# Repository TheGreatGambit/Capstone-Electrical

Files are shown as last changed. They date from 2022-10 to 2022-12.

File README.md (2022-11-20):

# The Great Gambit &mdash; Electrical

<!-- Buttons that link to the associated repos, uncomment all but this repo -->
<div align="center">
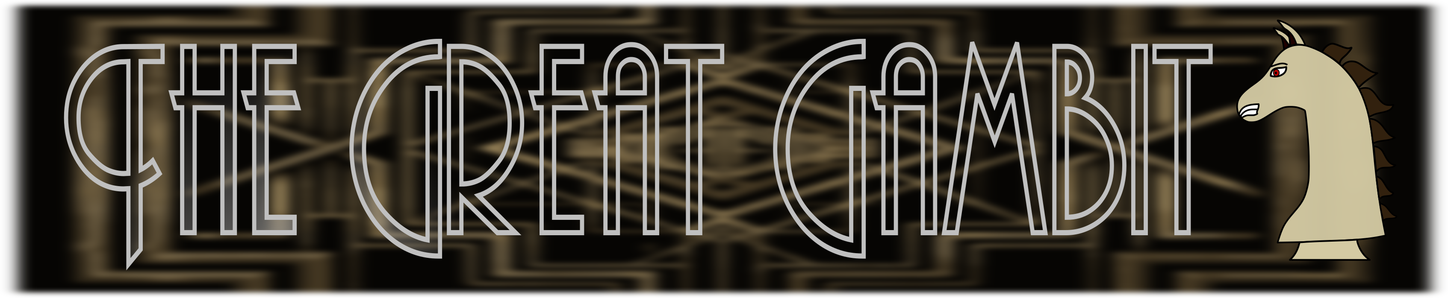
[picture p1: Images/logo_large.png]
The Great Gambit Logo
    
    <a href="https://cadlab.io/project/25988/main/files">
        CadLab Logo
    </a>
    <!-- <a href="https://github.com/TheGreatGambit/Capstone-Electrical">
        <img src="https://github.com/TheGreatGambit/Capstone-Electrical/blob/main/Images/logo_electrical_small.png" alt="Electrical Logo - Small" style="height:40px;width:200px">
    </a> -->
    <a href="https://github.com/TheGreatGambit/Capstone-Software">
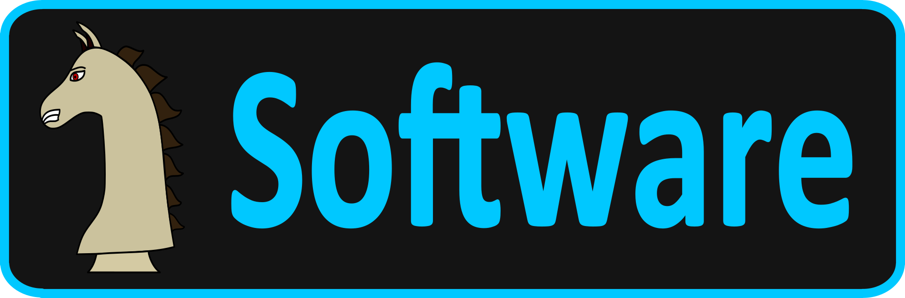
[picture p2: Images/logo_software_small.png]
Software Logo - Small
        
    </a>
    <a href="https://github.com/TheGreatGambit/Capstone-Mechanical-CAD">
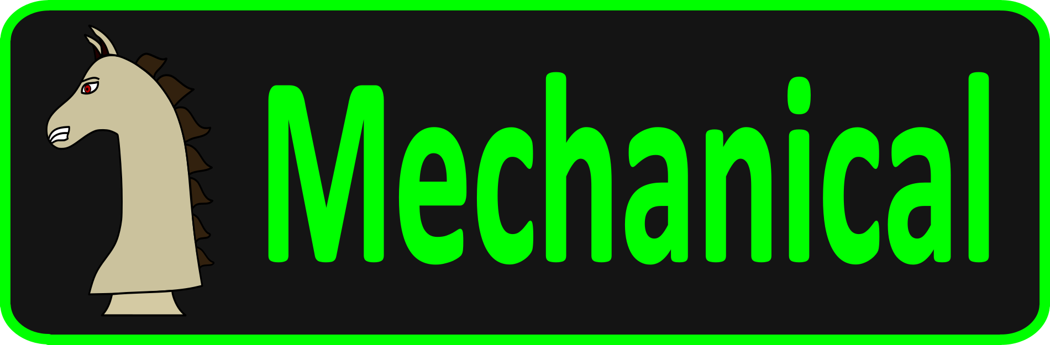
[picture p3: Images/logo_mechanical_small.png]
Mechanical Logo - Small
        
    </a>
    <a href="https://github.com/TheGreatGambit/Capstone-PyChess">
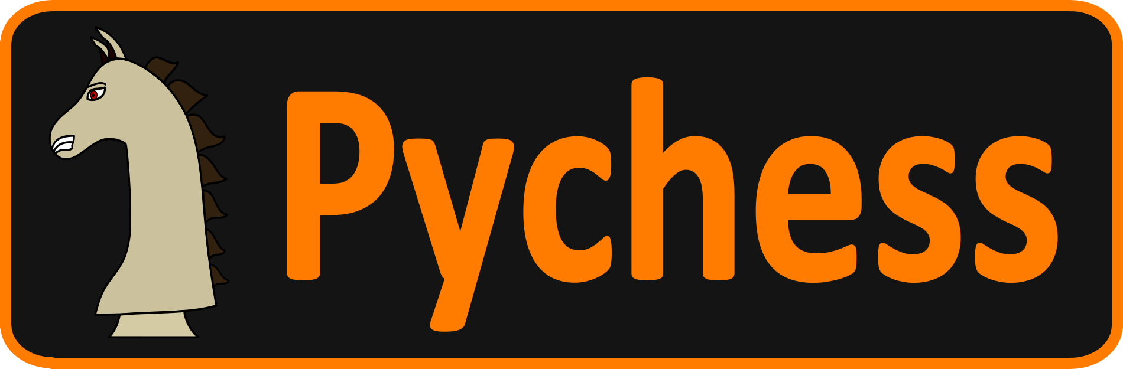
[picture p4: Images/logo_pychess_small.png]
PyChess Logo - Small
        
    </a>
</div>

<!-- Brief overview of this repo -->
## Overview
This project aims to create an autonomous robot capable of playing an intelligent, over-the-board game of chess against a human opponent. The system uses a three-axis, cantilevered, overhead gantry to move parallel to the chess board. Each axis is driven by a stepper motor, the horizontal axes using belts and the vertical axis using a rack and pinion. A crosspoint array of reed switches embedded in the physical chess board allows for piece detection, and with software record of the board state, piece recognition. This system is orchestrated by an [MSP432E401Y](https://www.ti.com/product/MSP432E401Y) microcontroller, with chess moves being pulled from the open-source [Stockfish](https://github.com/official-stockfish/Stockfish) chess engine, running on a [Raspberry Pi 3A+](https://www.raspberrypi.com/products/raspberry-pi-3-model-a-plus/). All communication between the Raspberry Pi and MSP432 is done through a universal asynchronous receiver-transmitter (UART) serial connection.

This repository contains all schematic and PCB files for the system, generated in [KiCad](https://www.kicad.org/). Files can be graphically viewed at [CADLab](https://cadlab.io/project/25988/main/files). In this document, `<LGR>` will indicate *your* local path to the GIT repo.

## Setup
1. Clone this repo onto your local machine.
2. Open `<LGR>/Boards/Main_Board/_Top_Level/Main_Board.kicad_pro` with KiCad to view the main project.
3. In KiCad, open `Main_Board.kicad_sch` to view the schematic, or `Main_Board.kicad_pcb` to view the PCB.

## Adding a Board (Project)
1. Create the following new directories:
    - `<LGR>/Boards/<YOUR_BOARD_NAME>`
    - `<LGR>/Boards/<YOUR_BOARD_NAME>/_DFM`
    - `<LGR>/Boards/<YOUR_BOARD_NAME>/_DFM/Gerber`
    - `<LGR>/Boards/<YOUR_BOARD_NAME>/_Top_Level`
2. Open KiCad
3. Select `File`->`New Project`
4. A `Create New Project` window will pop up. In the window, navigate to `<LGR>/Boards/<YOUR_BOARD_NAME>/_Top_Level`
5. Enter the file name `<YOUR_BOARD_NAME>.kicad_pro` and click `Save`

## Adding a Subsheet in an Existing Board
1. Create a new directory: `<LGR>/Boards/<YOUR_BOARD_NAME>/<SUBSHEET_NAME>`
2. Open `<LGR>/Boards/<YOUR_BOARD_NAME>/_Top_Level/<YOUR_BOARD_NAME>.kicad_sch` in the KiCad Schematic Editor
3. Select `Place`->`Add Sheet`
4. Click to place the symbol
5. A `Sheet Properties` window will pop up. Add the following entry:
    - Sheet Name: `<DESCRIPTIVE_NAME>`, Sheet File: `../<SUBSHEET_NAME>/<COMPONENT_NAME>.kicad_sch`
6. Right click the component and select `Import Sheet Pin` to place the hierarchical labels

## Installing External Libraries
*Note: We no longer use a custom path for project libraries. We instead use relative paths from `${KIPRJMOD}`*
1. **Install the library:**
    1. Download an external library
        - Ex: A model for the [DRV8824QPWPRQ1](https://www.mouser.com/ProductDetail/Texas-Instruments/DRV8824QPWPRQ1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) can be found under 'ECAD Model' 
    2. Unzip the download to get a `*.epw` file
    3. Download the [Library Loader](https://ms.componentsearchengine.com/pcb-libraries.php) tool from Mouser
    4. Register/login to the Library Loader tool
    5. Click `Open ECAD Model` and select the downloaded `*.epw` file
    6. By default the output is in `~/Downloads/LIB_GET.zip`. Unzip it
    7. Copy the unzipped contents into: `<LGR>/Project_Libraries/<LIBRARY_NAME>`
2. **Import the symbol:**
    1. In the KiCad Schematic Editor, go to: `Preferences`->`Manage Symbol Libraries`->`Project Specific Libraries`
    2. Add the following entry by clicking the `+` button:
        - Nickname: `<LIBRARY_NAME>`, Library Path: `${KIPRJMOD}/../../../Project_Libraries/<LIBRARY_NAME>/KiCad/<LIBRARY_NAME>.lib`
    3. Select `Migrate Libraries`
    4. Place the device in KiCad by going to `Place`->`Add Symbol` and search for `<LIBRARY_NAME>`
3. **Add the footprint:**
    1. In the KiCad PCB Editor, go to: `Preferences`->`Manage Footprint Libraries`->`Project Specific Libraries`
    2. Add the following entry by clicking the `+` button:
        - Nickname: `<LIBRARY_NAME>`, Library Path: `${KIPRJMOD}/../../../Project_Libraries/<LIBRARY_NAME>/KiCad`
4. **Update the symbol field to make exporting the BOM easier:**
    1. Right click on the symbol and click `Properties`
    2. Click `Edit Library Symbol`. This should open a symbol editing window.
    3. Go to `File -> Symbol Properties`
    4. Use the `+` button to add the fields `Datasheet`, `Manufacturer's Part Number`, `Digikey Part Number`, `Mouser Part Number`, `Digikey Link`, and `Mouser Link` in that order (with that exact spelling/capitalization)
        - The `Datasheet` should be a URL to the datasheet, and the `Digikey link` and `Mouser link` fields should be links to the part's product page
    5. Uncheck the `Show` field for everything except the `Reference` and `Value` fields
    6. If the part has a meaningful value (e.g., a 10k resistor), add that value in the `Value` field
    7. In the `Footprint` field, select the folder icon and search for `<LIBRARY_NAME>` in the popup
    8. Double click the result to associate the footprint you imported with the symbol you imported
        - Note: The footprint field might show something like `<LIBRARY_NAME>:<SEEMINGLY_RANDOM_STRING>`, this is okay
    7. Click `Ok` and close the library editor
    8. In the schematic, either right click the symbol and select `Update` or delete and re-add the symbol. The fields should now be included correctly

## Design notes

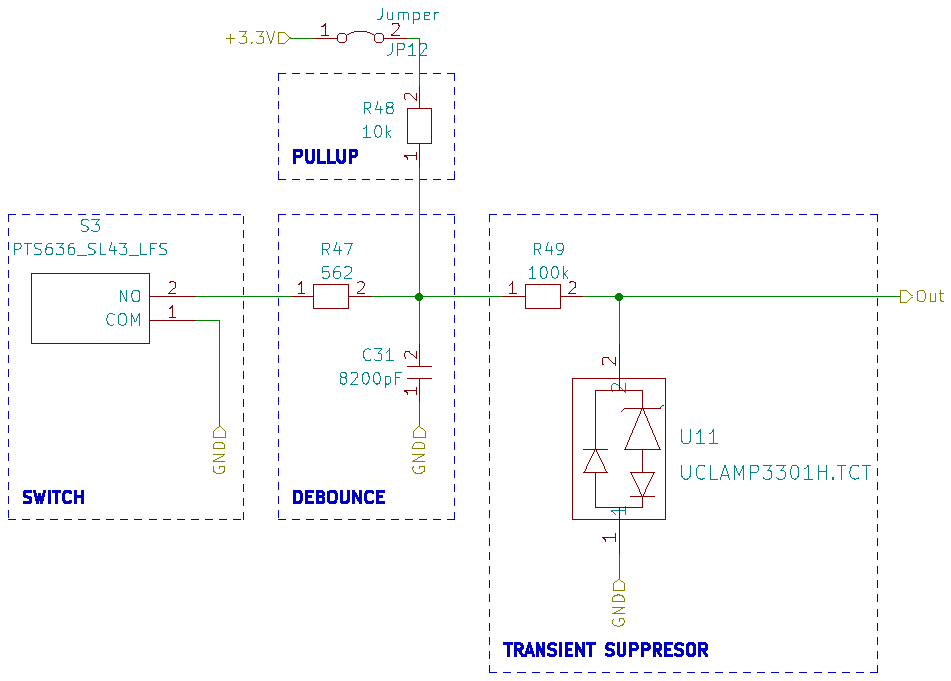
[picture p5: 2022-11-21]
Images/Main_Board/Button_Subsystem.PNG

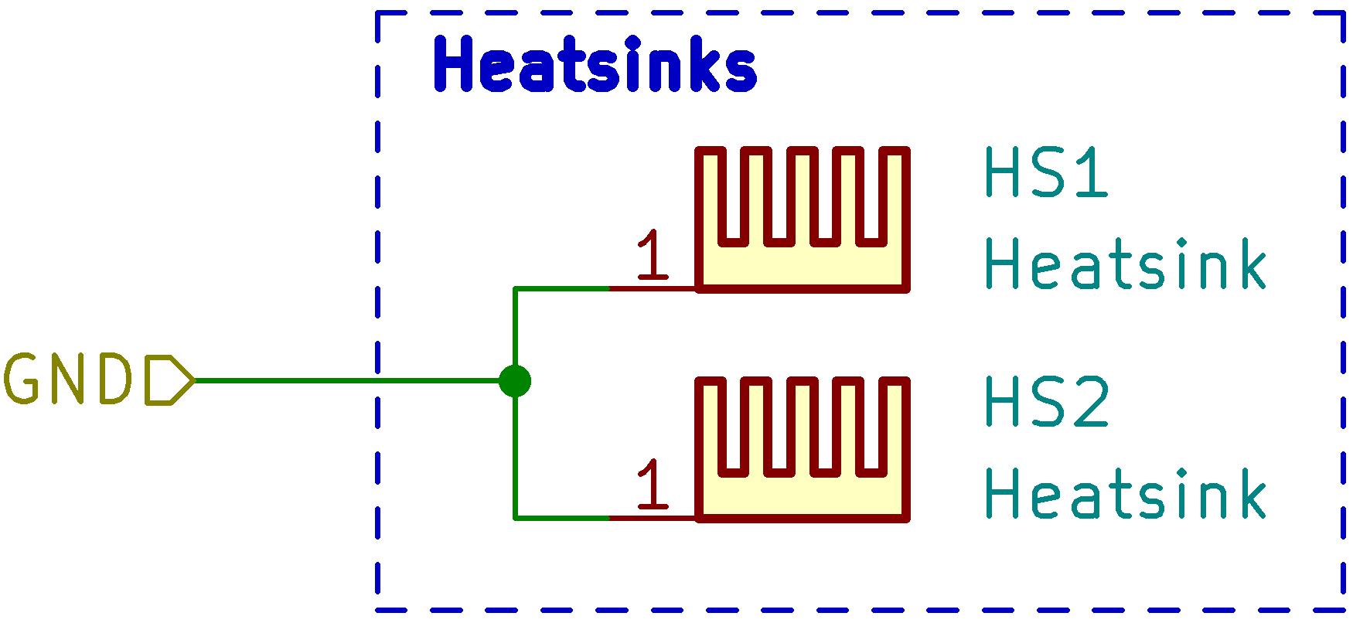
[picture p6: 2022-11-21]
Images/Main_Board/Heatsink_Subsystem.PNG

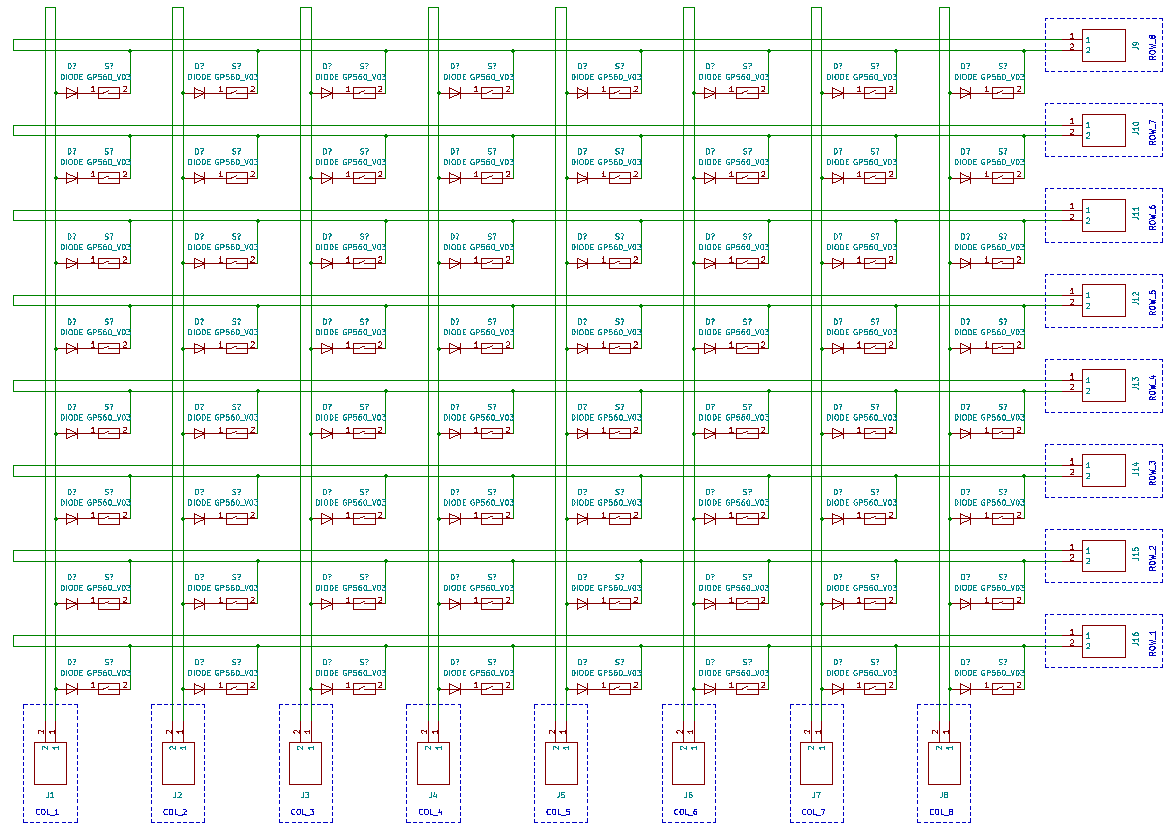
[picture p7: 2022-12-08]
Images/Sensor_Board_17x17/_Top_Level.PNG

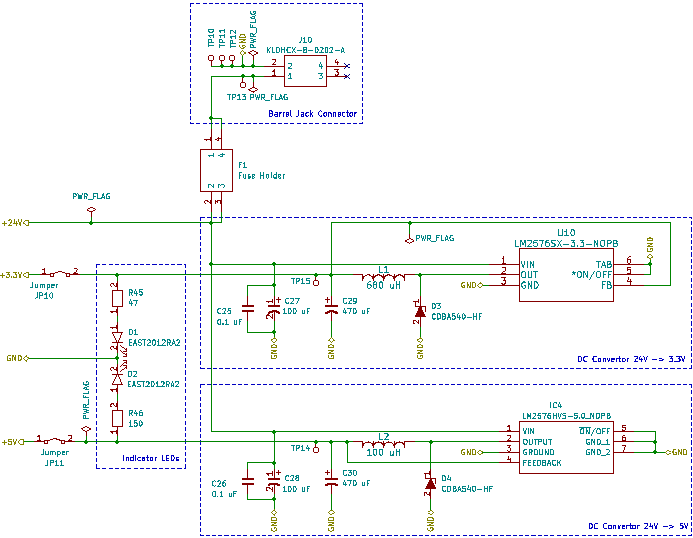
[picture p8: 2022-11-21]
Images/Main_Board/Power_Subsystem.PNG

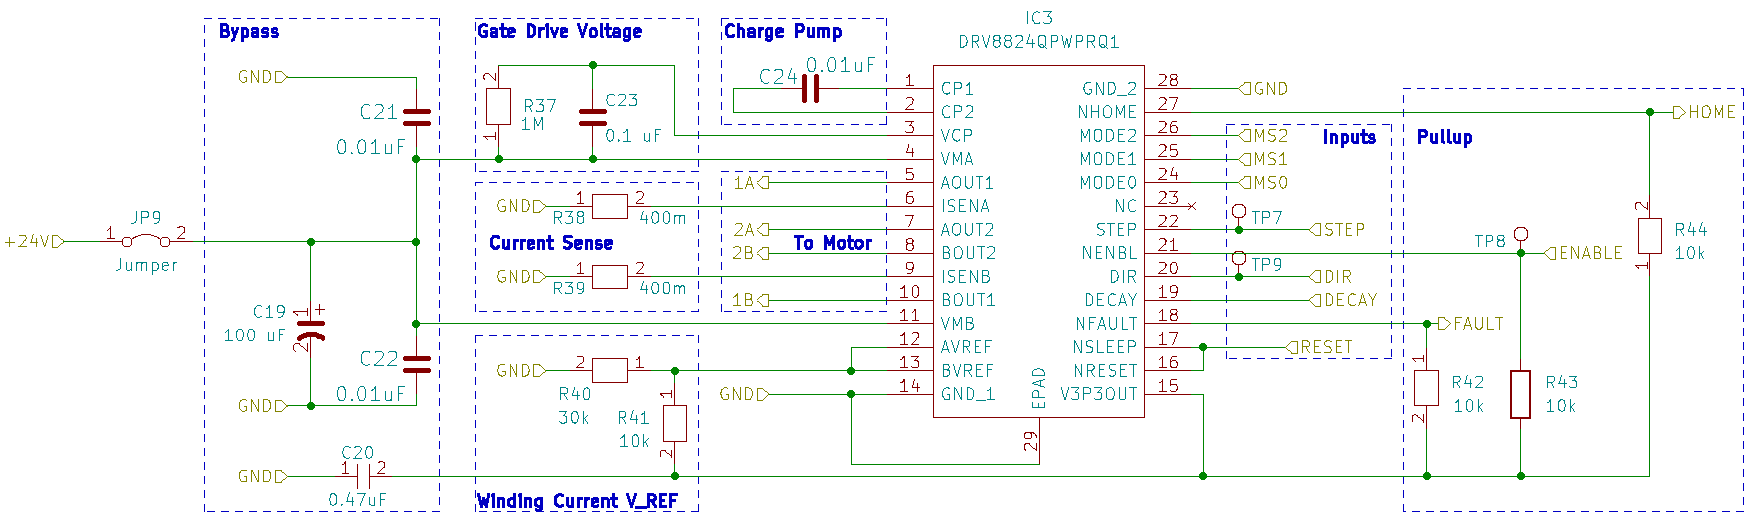
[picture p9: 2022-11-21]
Images/Main_Board/Stepper_Subsystem.PNG

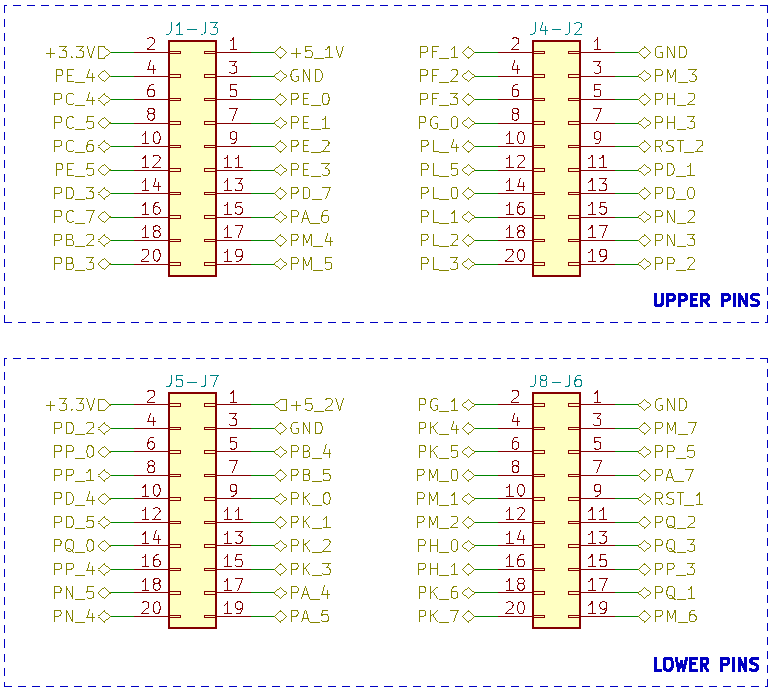
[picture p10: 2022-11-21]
Images/Main_Board/MSP_Subsystem.PNG

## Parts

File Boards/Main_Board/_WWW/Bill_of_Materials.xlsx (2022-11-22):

The Great Gambit PCB
REV 21
Line | Quantity | Reference | Value | MANU PART # | MANU
1 | 5 | C1, C7, C19, C27, C28 | 100 uF | 860020573008 | Würth Elektronik
2 | 3 | C2, C8, C20 | 0.47uF | C1812X474K2RACAUTO | KEMET
3 | 8 | C5, C11, C23, C25, C26, C33-C35 | 0.1 uF | CL10B104KB8NNNC | Samsung Electro-Mechanics
4 | 9 | C3, C4, C6, C9, C10, C12, C21, C22, C24 | 0.01uF | CK05BX103K | KYOCERA AVX
5 | 12 | C13, C14, C15, C16, C17, C18, C31, C32, C37-C40 | 8200pF | C1210C822K2RACAUTO | KEMET
6 | 3 | C29, C30, C36 | 470 uF | EEE-FP1E471AP | Panasonic Electronic Components
7 | 2 | D1, D2 |  | EAST2012RA2 | Everlight Electronics Co Ltd
8 | 2 | D3, D4 |  | CDBA540-HF | Comchip Technology
9 | 1 | F1 |  | 3588 | Keystone Electronics
10 | 2 | HS1, HS2 |  | ATS-52150P-C1-R0 | Advanced Thermal Solutions Inc.
11 | 3 | IC1-IC3 |  | DRV8824QPWPRQ1 | Texas Instruments
12 | 1 | IC4 |  | LM2576HVS-5.0/NOPB | Texas Instruments
13 | 1 | IC5 |  | BD62130AEFJ-E2 | Rohm Semiconductor
14 | 1 | J1 | DNI | 302-S101 | On Shore Technology Inc.
15 | 10 | J2, J7-J9, J11, J20-J24 | DNI | OQ0212500000G | Amphenol Anytek
16 | 11 | J3, J4, J5, J12, J13, J14, J15, J16, J17, J18, J19 | DNI | OQ0432500000G | Amphenol Anytek
17 | 4 | J1-J3, J4-J2, J5-J7, J8-J6 | DNI | PPTC102LFBN-RC | Sullins Connector Solutions
18 | 1 | J6 | DNI | USB1130-15-A | GCT
19 | 1 | J10 | DNI | KLDHCX-8-0202-A | Kycon, Inc.
20 | 21 | JP1, JP2, JP3, JP4, JP5, JP6, JP7, JP8, JP9, JP10, JP11, JP12, JP13, JP14, JP15, JP16, JP17, JP18, JP19, JP20, JP21 | DNI | PH1-02-UA | Adam Tech
21 | 1 | L1 | 680 uH | SRR1210-681M | Bourns Inc.
22 | 1 | L2 | 100 uH | PA4344.104NLT | Pulse Electronics
23 | 1 | LED1 |  | HV-5RGB25 | Inolux
24 | 3 | R1, R9, R37 | 1M | TNPV08051M00BEEA | Vishay Dale
25 | 6 | R2, R3, R10, R11, R38, R39 | 400m | WSL2010R4000FEA | Vishay Dale
26 | 3 | R4, R12, R40 | 30k | ERJ-PB6B3002V | Panasonic Electronic Components
27 | 37 | R5, R6, R8, R13, R14, R16, R20, R23, R26, R29, R32, R35, R41, R42, R44, R48, R51, R58-R73, R75, R78, R81, R84 | 10k | RMCF1206FT10K0 | Stackpole Electronics Inc
28 | 3 | R7, R15, R43 | 10k
29 | 2 | R17, R18 | 2.2 k | CF14JT2K20 | Stackpole Electronics Inc
30 | 12 | R19, R22, R25, R28, R31, R34, R47, R50, R74, R77, R80, R83 | 562 | CR0402-FX-5620GLF | Bourns Inc.
31 | 12 | R21, R24, R27, R30, R33, R36, R49, R52, R76, R79, R82, R85 | 100k | RCV2512100KFKEGAT | Vishay Dale
32 | 1 | R45 | 47 | CHP2512AFX-47R0ELF | Bourns Inc.
33 | 1 | R46 | 150 | SDR03EZPF1500 | Rohm Semiconductor
34 | 5 | R53, R54, R55, R56, R57 | 270 | SDR10EZPJ271 | Rohm Semiconductor
35 | 1 | R86 | 1.2k
36 | 3 | S1, S2, S3 |  | PTS636 SL43 LFS | C&K
37 | 17 | TP1, TP2, TP3, TP4, TP5, TP6, TP7, TP8, TP9, TP10, TP11, TP12, TP13, TP14, TP15, TP16, TP17 | DNI | 5010 | Keystone Electronics
38 | 16 | U1, U2, U3, U4, U5, U6, U8, U9, U11, U12, U13, U14, U17, U18, U19, U20 |  | UCLAMP3301H.TCT | Semtech Corporation
39 | 1 | U7 |  | JS102011SCQN | C&K
40 | 1 | U10 |  | LM2576SX-3.3/NOPB | Texas Instruments
41 | 2 | U15, U16 |  | SN74LV4051ATPWRQ1 | Texas Instruments
42 | 1 | U21 |  | RUC002N05T116 | Rohm Semiconductor

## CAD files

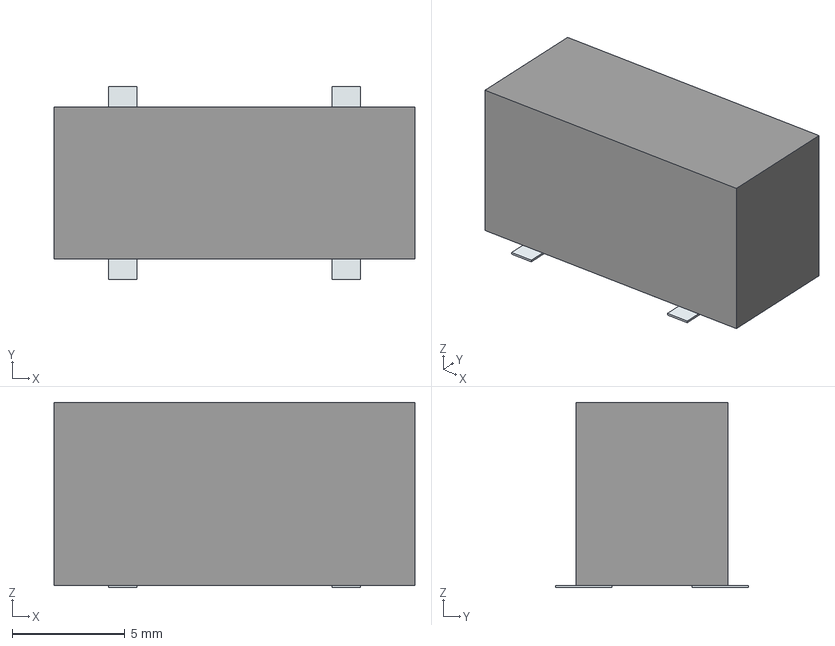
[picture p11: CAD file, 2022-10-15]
Project_Libraries/3588/3588/3D/3588.stp
16.0 x 8.57 x 8.22 mm
Pins

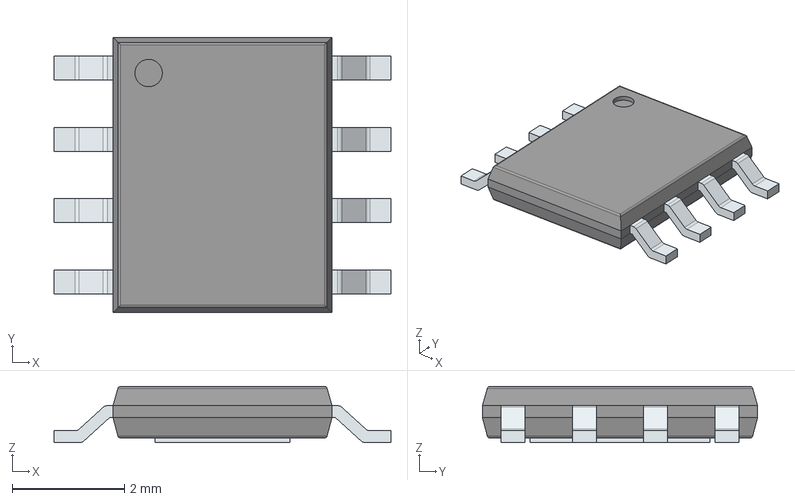
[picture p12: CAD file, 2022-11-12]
Project_Libraries/BD62130AEFJ-E2/BD62130AEFJ-E2/3D/BD62130AEFJ-E2.stp
6.00 x 4.90 x 1.00 mm
PinsArrayLR
ThermalPad

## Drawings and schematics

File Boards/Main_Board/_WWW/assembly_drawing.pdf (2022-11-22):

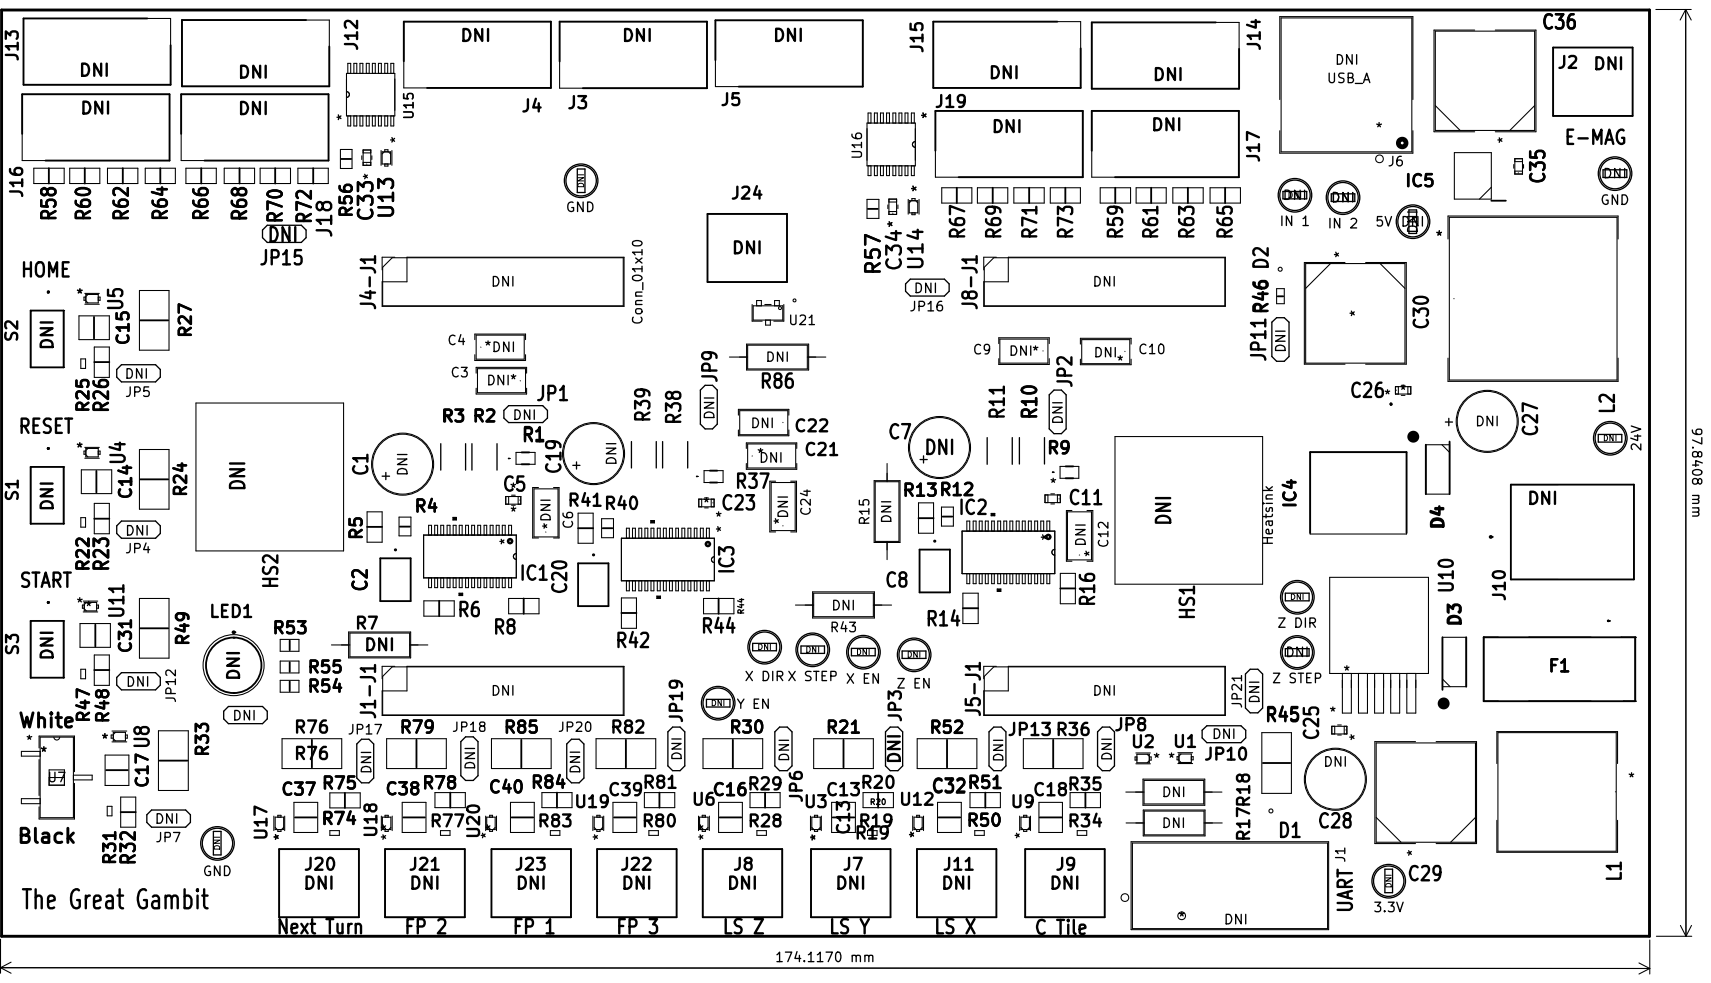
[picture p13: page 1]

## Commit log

2022-10-03 Break top level scheamtic into subsystems. Use DRV8824-Q1 driver chip. Document setup
    [Button.kicad_sch, Button_Template.kicad_sch, Buttons_Full.kicad_sch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]
2022-10-04 Worked on Power supply subsheet
    [Button.kicad_sch, EDI2CAP.CFG, KLDHCX-8-0202-A.stp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]
2022-10-04 Finalize MSP432, stepper, and button subsheets
    [Button.kicad_sch, EDI2CAP.CFG, LED.kicad_sch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]
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2022-10-04 Add gitignore, fix stepper subsystem
    [LED.kicad_sch, Stepper_Driver.kicad_sch, Top_Level.kicad_sch]
2022-10-04 Changed the DC convertor circuit
    [PowerSupply.kicad_sch]
2022-10-04 Add digikey/mouser components to stepper and button subsystems
    [Button.kicad_sch, C1210C822K2RACAUTO.stp, C1812X474K2RACAUTO.stp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]
2022-10-05 Added specific components for the power subsheet
    [PowerSupply.kicad_sch, Top_Level.kicad_sch]
2022-10-06 PA4 and PA5 reserved for U3RX and U3TX in top-level schematic
    [Top_Level.kicad_sch]
2022-10-09 Fix LED subsystem, cut unnecessary GPIO connections, add sheets for remaining subsystems
    [EDI2CAP.CFG, Electromagnet.kicad_sch, LED.kicad_sch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]
2022-10-09 Switched the pins on the barrel jack connector
    [Button.kicad_sch, LED.kicad_sch, PowerSupply.kicad_sch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]
2022-10-09 Added footprint for the switches
    [Button.kicad_sch, Top_Level.kicad_pcb, Top_Level.kicad_sch]
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2022-10-09 Fix all footprints and symbols, import to PCB
    [PowerSupply.kicad_sch, Top_Level.kicad_pcb, Top_Level.kicad_sch]
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2022-10-09 Added circuitry for the Pi subsystem
    [Button.kicad_sch, PiConnector.kicad_sch, Stepper_Driver.kicad_sch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]
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2022-10-09 Fix MSP connector spacing
    [Button.kicad_sch, LED.kicad_sch, LimitSwitch.kicad_sch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]
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2022-10-10 placed switched + buttons
    [Top_Level.kicad_pcb]
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2022-10-12 Cleanup files so ERC passes
    [Button.kicad_sch, LimitSwitch.kicad_sch, MSP432E401Y.kicad_sch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]
2022-10-12 Fixed entire BOM for all components
    [Button.kicad_sch, LED.kicad_sch, LimitSwitch.kicad_sch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]
2022-10-12 Adjusted the Pi subsystem
    [Button.kicad_sch, LimitSwitch.kicad_sch, MSP432E401Y.kicad_sch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]
2022-10-12 Fix annotations, add test points
    [Button.kicad_sch, LED.kicad_sch, LimitSwitch.kicad_sch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]
2022-10-12 Add screenshots of each subsystem
    [Button.kicad_sch, LimitSwitch.kicad_sch, MSP432E401Y.kicad_sch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]
2022-10-15 Added 5V power supply
    [Button.kicad_sch, CDBA540-HF.stp, LimitSwitch.kicad_sch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]
2022-10-15 Added extra bypass caps to the power supply
    [Button.kicad_sch, LimitSwitch.kicad_sch, PowerSupply.kicad_sch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]
2022-10-15 Added a fuse and fixed ERC
    [3588.stp, Button.kicad_sch, LimitSwitch.kicad_sch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]
2022-10-15 Added jumpers to the 3.3 and 5V lines
    [PiConnector.kicad_sch, PowerSupply.kicad_sch, Stepper_Driver.kicad_sch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]
2022-10-15 Redo sensor network, redo MSP432 connections, redo LED subsystem, add shunts throughout, ERC still passes
    [Button.kicad_sch, LED.kicad_sch, LimitSwitch.kicad_sch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]
2022-10-15 Added LEDs to the power supply
    [Button.kicad_sch, LimitSwitch.kicad_sch, PowerSupply.kicad_sch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]
2022-10-16 Added electromagnet circuit and adjusted the bypass caps
    [DRV8210DRLR.stp, Electromagnet.kicad_sch, PowerSupply.kicad_sch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]
2022-10-16 Resolve misconfigured components, replace PCB from now completed schematic
    [Button.kicad_sch, Electromagnet.kicad_sch, LED.kicad_sch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]
2022-10-16 Swapped pins on the barrel jack
    [Button.kicad_sch, LimitSwitch.kicad_sch, PowerSupply.kicad_sch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]
2022-10-16 Layed out power supply
    [LimitSwitch.kicad_sch, Stepper_Driver.kicad_sch, Top_Level.kicad_pcb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]
2022-10-21 Added USB connector for the pi
    [Button.kicad_sch, LimitSwitch.kicad_sch, Stepper_Driver.kicad_sch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]
2022-10-21 Swapped TVS Diodes
    [Button.kicad_sch, LimitSwitch.kicad_sch, PiConnector.kicad_sch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]
2022-10-21 Relayed out the power supply and stepper drivers
    [Button.kicad_sch, LimitSwitch.kicad_sch, PiConnector.kicad_sch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]
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2022-10-21 Layed out stepper connectors and test points
    [PiConnector.kicad_sch, Top_Level.kicad_pcb, Top_Level.kicad_sch]
2022-10-22 Redo pinout, finish pcb layout (no traces)
    [Button.kicad_sch, Electromagnet.kicad_sch, LED.kicad_sch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]
2022-10-23 Add GND plane, GND major ICs
    [Top_Level.kicad_pcb]
2022-10-23 Adjust stepper placement for heatsinks
    [Top_Level.kicad_pcb]
2022-10-25 Added heatsink footprints in approx. location
    [Top_Level.kicad_pcb]
2022-10-26 Flipped the MSP headers
    [MSP432E401Y.kicad_sch, Top_Level.kicad_pcb, Top_Level.kicad_sch]
2022-10-26 Reordered the sensor network to shorten traces
    [Top_Level.kicad_pcb, Top_Level.kicad_sch]
2022-10-26 Fixed footprint courtyard issues (mostly)
    [Button.kicad_sch, Electromagnet.kicad_sch, LimitSwitch.kicad_sch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]
2022-10-26 Redid the stepper drivers to adhere to TI's layout directions
    [Stepper_Driver.kicad_sch, Top_Level.kicad_pcb, Top_Level.kicad_sch]
2022-10-27 Fix vias for Analog Digital's requirements
    [Button.kicad_sch, Electromagnet.kicad_sch, LimitSwitch.kicad_sch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]
2022-10-27 Fix stepper driver footprints
    [Stepper_Driver.kicad_sch, Top_Level.kicad_pcb, Top_Level.kicad_sch]
2022-10-27 Added stepper traces to connectors
    [Top_Level.kicad_pcb]
2022-10-28 Layed out the user buttons
    [Switch.kicad_sch, Top_Level.kicad_pcb]
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2022-10-28 Placed all the protection components
    [Button.kicad_sch, Electromagnet.kicad_sch, LimitSwitch.kicad_sch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]
2022-10-28 Rearranged connectors to shorten traces
    [Top_Level.kicad_pcb]
2022-10-28 Moved some pins to make routing easier
    [Top_Level.kicad_pcb, Top_Level.kicad_sch]
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2022-10-28 Adjustments in prep for silkscreen
    [Top_Level.kicad_pcb, Top_Level.kicad_sch]
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2022-10-28 Only the truly awful traces left
    [Top_Level.kicad_pcb, Top_Level.kicad_sch]
2022-10-28 KiCad keeps crashing and getting rid of silkscreen
    [Top_Level.kicad_pcb, Top_Level.kicad_sch]
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2022-10-28 All major traces done
    [Top_Level.kicad_pcb, Top_Level.kicad_sch]
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2022-10-28 Finish traces, fix DRC, add gerbers
    [Top_Level.kicad_pcb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]
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2022-10-28 Added polarity to capacitor silkscreens
    [Top_Level.kicad_pcb]
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2022-10-28 Smaller pads on the LED
    [Top_Level.kicad_pcb]
2022-10-28 Silkscreen fixes
    [Top_Level.kicad_pcb]
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2022-10-28 4th times the charm
    [Top_Level.kicad_pcb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]
2022-10-29 New try at FreeDFM
    [Top_Level.kicad_pcb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]
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2022-10-30 Spaced out vias. No show stoppers
    [Top_Level.kicad_pcb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]
2022-10-30 Corrections to the power supply
    [MSP432E401Y.kicad_sch, PowerSupply.kicad_sch, Top_Level.kicad_pcb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]
2022-10-30 Swapped resistors in stepper driver
    [Electromagnet.kicad_sch, PiConnector.kicad_sch, PowerSupply.kicad_sch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]
2022-10-30 Fixed the barrel jack footprint
    [Top_Level.kicad_pcb]
2022-10-30 Changed Pi resistors back to through hole
    [PiConnector.kicad_sch, PowerSupply.kicad_sch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]
2022-10-30 Last? Submission to FreeDFM
    [Top_Level-job.gbrjob]
2022-11-09 Updates from meeting with Powell
    [Top_Level.kicad_pcb]
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2022-11-10 Working on power supply
    [Top_Level.kicad_pcb, Top_Level.kicad_sch]
2022-11-10 Added signal light MOSFET
    [PowerSupply.kicad_sch, Signal_Light.kicad_sch, Stepper_Driver.kicad_sch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]
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2022-11-12 Replace small resistors/capacitors with through-hole; fix DRC aside from electromagnet and MUXes
    [Button.kicad_sch, LED.kicad_sch, LimitSwitch.kicad_sch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]
2022-11-12 Replace MUX/DEMUX; DRC passes aside from electromagnet
    [Electromagnet.kicad_sch, LimitSwitch.kicad_sch, SensorNetwork.kicad_sch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]
2022-11-12 Replaced electromagnet IC and fixed ERC errors with stepper driver
    [BD62130AEFJ-E2.stp, Electromagnet.kicad_sch, SensorNetwork.kicad_sch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]
2022-11-12 Added traces for emag and increased the width of some power lines
    [Electromagnet.kicad_sch, PiConnector.kicad_sch, SensorNetwork.kicad_sch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]
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2022-11-12 Updated GND wires on e mag IC
    [Top_Level.kicad_pcb]
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2022-11-13 Fixed TVS diode pin 1 markers
    [Top_Level.kicad_pcb]
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2022-11-13 Small trace fix. Still has problems
    [Top_Level.kicad_pcb]
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2022-11-13 power barrel jack connector footprint
    [Top_Level.kicad_pcb]
2022-11-13 Fixed UART connections
    [PiConnector.kicad_sch, SensorNetwork.kicad_sch, Top_Level.kicad_pcb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]
2022-11-13 Fixed UART on the PCB
    [Top_Level.kicad_pcb]
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2022-11-19 Fixed ground
    [8x1.kicad_pcb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]
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2022-11-21 Correct spacing on sensor board, refactor datasheets and project libraries
    [Button.kicad_sch, DRV8210DRLR.stp, Electromagnet.kicad_sch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]
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2022-11-22 Update Gabi's 2x8 board and resolve Git issues
    [Bill_of_Materials.xlsx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]
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2022-12-13 Fix typos
    [MSP432E401Y.kicad_sch, Main_Board.kicad_sch, SensorNetwork.kicad_sch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]
